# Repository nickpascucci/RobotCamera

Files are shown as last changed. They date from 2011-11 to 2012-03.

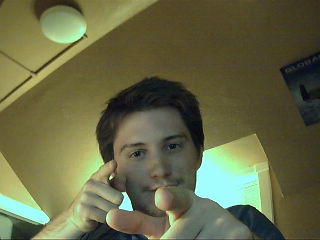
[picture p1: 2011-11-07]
src/victory.jpg

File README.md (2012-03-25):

## Robot Camera

# Overview
This project is aimed at creating a simple rover robot which can use a camera to
identify navigational cues and interesting features when negotiating a maze.

The project consists of a) a set of CAD files used for fabricating the robot's
chasis, and b) source code for motion control, vision, remote operation, and
autonomous navigation.

# Bill of Materials
### Parts:
+ 4 8"x0.75" aluminum right angle extrusion
+ 8 4"x0.75" aluminum right angle extrusion
+ 84 M2.5 x 10 Socket head cap screws
+ 8 M2.5 x 20 Socket head cap screws
+ 92 M2.5 Nuts
+ 1 PandaBoard, with SD card
+ 1 Arduino
+ 2 Continuous rotation servos
+ 2 P1230 Photogates & supporting hardware (refer to your photogate's datasheet.)
+ 1 USB webcam (I used a V7 CS2021.)

### Tools:
+ 3D printer (I recommend using FDM'd ABS for this for its mechanical qualities.)
+ Drill press
+ Soldering iron
+ Tweezers (highly recommended for both soldering and tightening fasteners.)

# How to build this crazy thing
Ok, so you want to build your own robot. How do you get started?

### Structure
First, you're going to need a chasis. There's no reason you have to use mine
versus building your own, but in case you do, all the files you need should be
in the *draw/* directory. All of the parts except for angle aluminum and
fasteners are available as .stl meshes, ready and tested for 3D printing. Most
are also provided as STEP files that can be imported into all major CAD systems
and modified to suit your needs. You'll also need to cut and drill some pieces
of angle aluminum to serve as the primary structural members. I've included
drawings of these parts to give you the right dimensions. All of it goes
together as an assembly as detailed in the assembly.pdf drawing.

### Motion
Great, you have a chassis to hold everything in place. Now you're going to need
some electronics to drive it! The "ServoBracket.{step, stl}" parts are designed
to hold a standard size servo. Of course, a standard servo won't work for
turning wheels; you'll need continuous rotation ones. Mount two of them in the
brackets. In order to keep track of distance traveled and current speed
settings, you'll need to have some kind of encoder on your wheels. I designed a
3D-printable encoder wheel that sits between the servo and the drive wheel. It's
designed to fit into a P1230 photogate, though it should fit others as
well. These can be slotted into the smaller holes on the servo bracket and glued
into place with a 2-part epoxy. Connect the servos and photogates to an Arduino,
modify the firmware to match your pin choices, and upload the
firmware. Congrats, you have a simple motion control system!

### Intelligence
Next comes the brains of the operation. I assume that you made 3 of the board
mount assemblies; if not, do so now. These have little arms that rotate to meet
up with holes in the PandaBoard. Mount your board in the most convenient
orientation; I decided to put the USB ports forward. Attach the Arduino via USB
to the board, and do the same for your webcam. There is a part for mounting a V7
webcam to the chasis; if you have a similar device it should work well, and if
not you'll have to design your own. Attach your webcam to the chasis.

### Software
All right, that just about covers the hardware! Next step, software.

I'll assume that you have a working Linux distribution on your
PandaBoard. You're going to need to install Python (2.7 is preferred), OpenCV
and its Python bindings, PySerial, and Git. Clone this repo onto the PandaBoard,
check that settings.py reflects your configuration, and start up BotDriver. It
will attach to the network interface and wait for a connection from Pilot. On
your control machine, start a Processing session and initiate a Pilot run. Enter
the IP address of the robot and hit "Connect". If everything's working, it
should start feeding you video and relaying your commands to the robot. If not,
something went wrong; look at the output of both Pilot and BotDriver to see if
either of them has any useful information. If not, feel free to get in contact
with me.

## Misc

I'm open to incorporating updates or changes to any of this software/hardware;
if you make any improvements, I'd love to hear about them! If they have any
chance of being useful for other people, send me a pull request and I'll try and
merge them.

## Wishlist
See the issue tracker.

## LICENSE
All of the code in this repository is free software, licensed under the GNU
GPL. If you'd like an alternative license, contact me and we'll work something
out.

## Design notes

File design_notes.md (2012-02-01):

# Design Notes

## Overview

## Hardware Design

### 1) Structure

The system is designed to be constructed from a set of aluminum angle pieces fastened together into
a rectangular box configuration using 3D printed brackets. The source file for these brackets is
available in the draw/ directory. This configuration is straightforward to fabricate and offers
flexibility to the design, as well as an acceptable level of rigidity and ease of modification. 4-40
x 1/2" socket head screws are used as fasteners due to their high availability and their
standardization in mounting circuit boards. Mounting points are provided by additional 3D printed
parts and flat surfaces are fabricated from sheets of acrylic mounted to the frame.

### 2) Locomotion

Movement is accomplished through the use of full rotation servomotors. These motors allow the user
to set a constant angular velocity at the servo shaft via a PWM signal, and are thus useful for
robotics due to their lowered complexity of control. Custom brackets fabricated on a 3D printer are
used to fasten the motors to the frame, and they are controlled by an Arduino microcontroller to
provide a level of abstraction to the main navigation systems.

### 3) Sensing

The system is equipped with several sensors: first, a set of optical rotary encoders measures the
travel of each wheel and reports this data to the Arduino motor controller. This allows the motor
controller to maintain a constant velocity and to record the distance traveled by each wheel,
enabling dead-reckoning position estimates to be performed. Second, a powerful camera assembly is
mounted to the front frame of the robot which provides 640x480 pixel images for use in navigation
and object detection. Image data is transmitted over a serial communications link directly to the
PandaBoard controller, and images can be captured about once every 3 seconds.

### 4) Power Supply

Design of the power supply is ongoing... I've tried using a portable device charger to supply power
over USB, but the PandaBoard draws more current than it can provide and can't complete the boot
sequence. I may combine two such chargers to power the system.

## Software Design
   .......................       ......................
   .                     .       .    Internal        .
   . Input/Sensor Module .........   State Module     .
   .                     .       .  (Kalman Filter)   .
   .......................       ......................
             .                             .
             .                             .
   .......................       ......................         .......................
   .   World State       .       .   Decision         .         .     Actuator        .
   .    Module           .........    Module          ...........      Module         .
   .......................       ......................         .......................

## Notes

- The camera selected for this project was chosen due to its serial communications
  capabilities. Originally, the entire system was to be operated by a Parallax Propeller
  microcontroller; however, the computational requirements of computer vision proved to be too great
  for that system and it was decided to upgrade to a PandaBoard. By that time a camera had already
  been purchased, and the system has been designed to work with it.

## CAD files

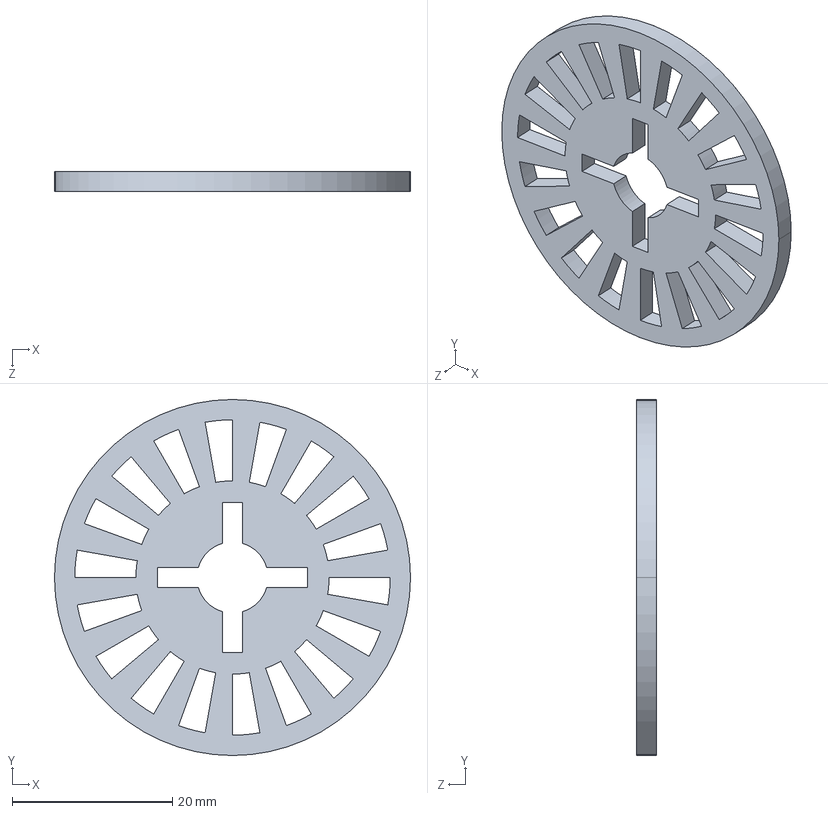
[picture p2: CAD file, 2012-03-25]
draw/step/EncoderWheel.STEP
44.4 x 44.4 x 2.54 mm

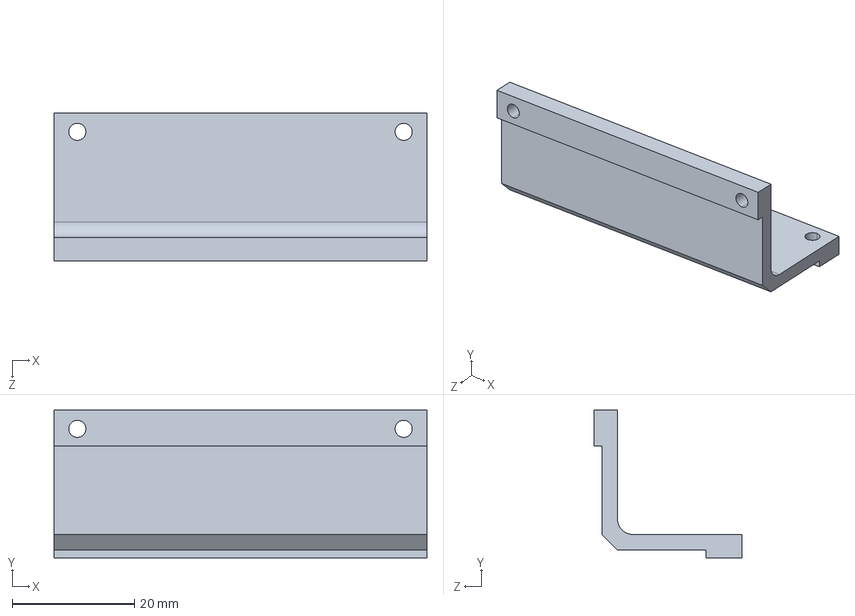
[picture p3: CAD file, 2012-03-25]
draw/step/ServoBracketClamp.STEP
61.0 x 24.1 x 24.1 mm

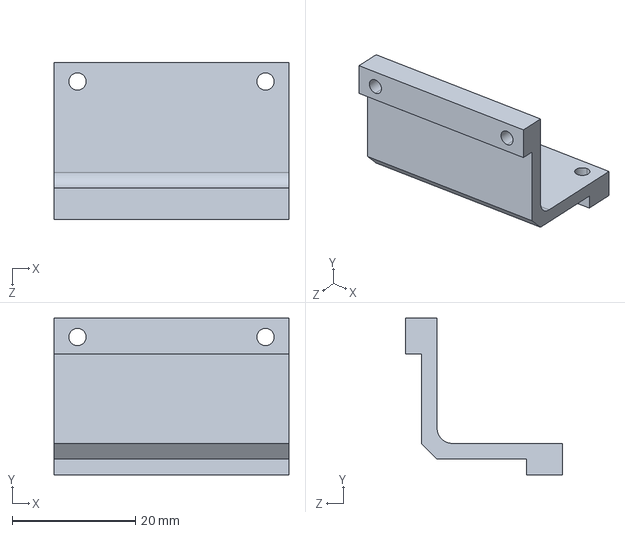
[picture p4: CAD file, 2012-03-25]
draw/step/PartBracketClamp.STEP
38.1 x 25.4 x 25.4 mm

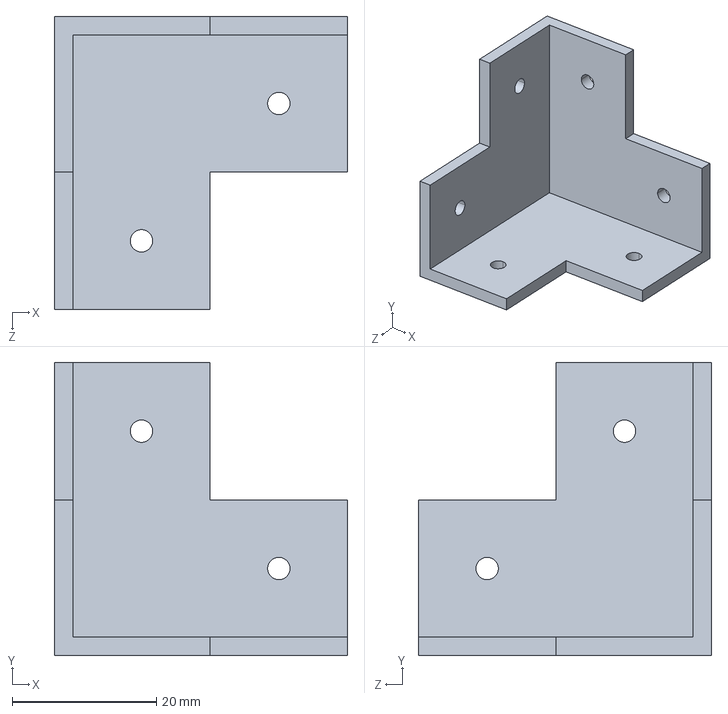
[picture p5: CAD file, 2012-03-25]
draw/step/CornerBracket.STEP
40.6 x 40.6 x 40.6 mm

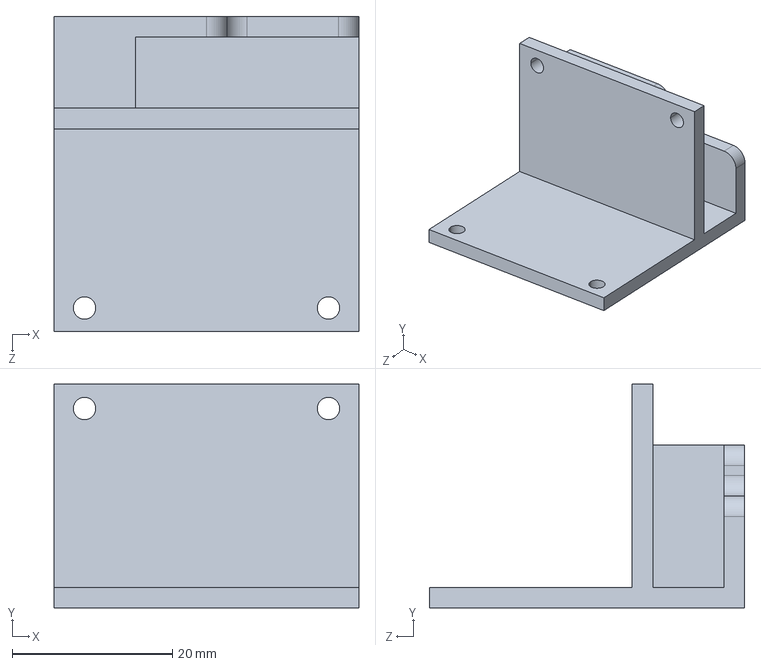
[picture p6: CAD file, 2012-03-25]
draw/step/CameraBracket.STEP
38.1 x 27.9 x 39.4 mm

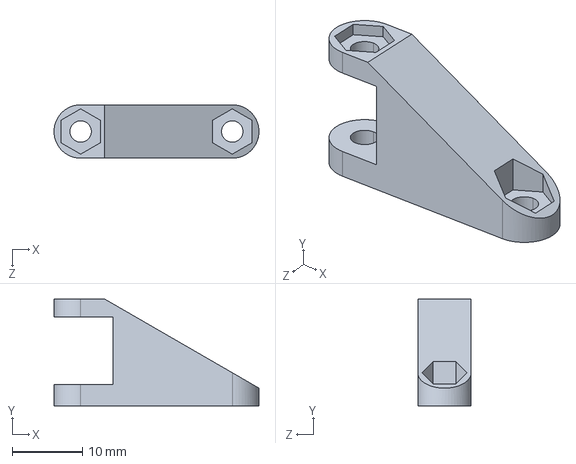
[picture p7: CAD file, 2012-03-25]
draw/step/BoardMountingArm.STEP
29.2 x 15.2 x 7.62 mm

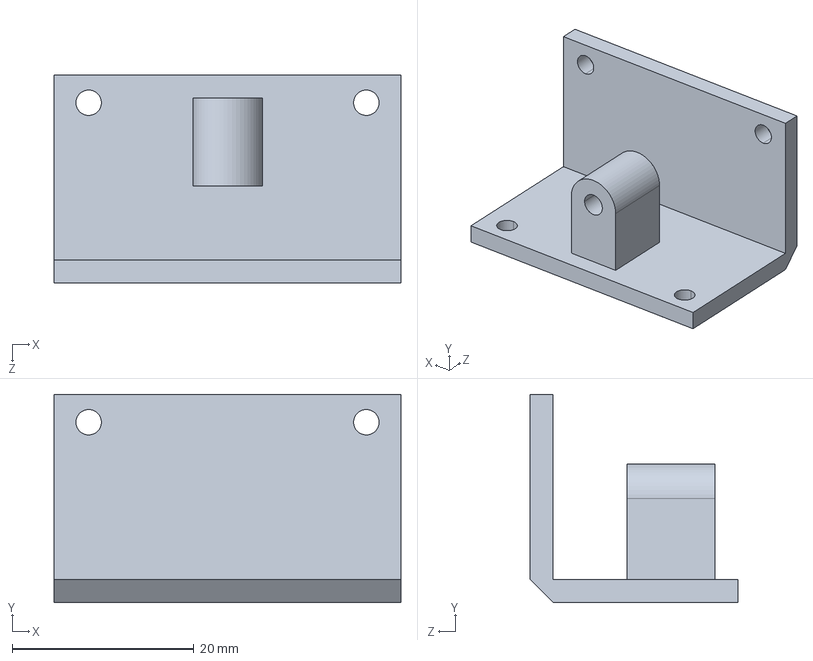
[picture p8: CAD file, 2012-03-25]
draw/step/BoardMountingClamp.STEP
38.1 x 22.9 x 22.9 mm

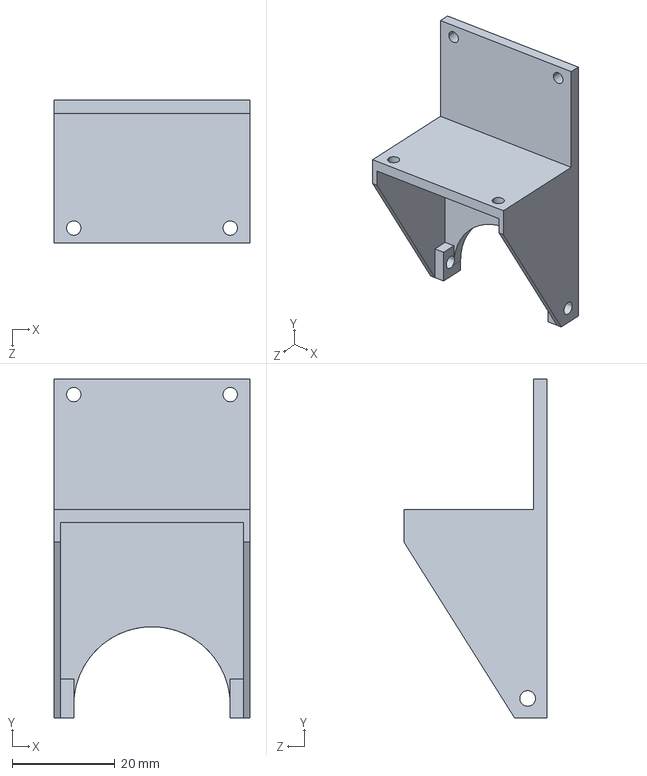
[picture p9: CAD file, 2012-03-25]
draw/step/CasterBracket.STEP
38.1 x 66.0 x 27.9 mm

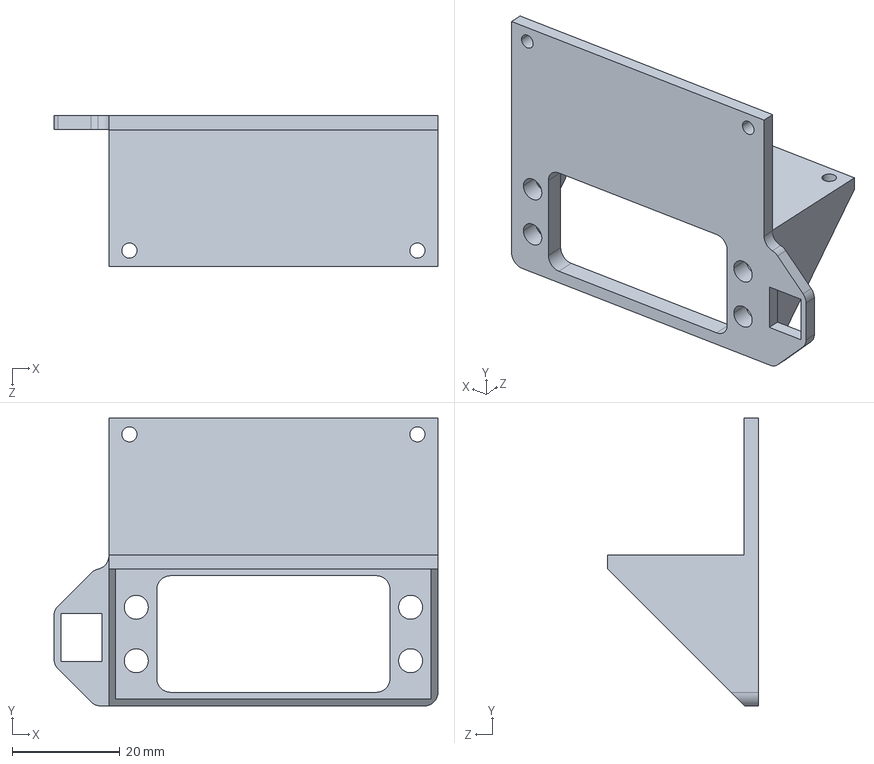
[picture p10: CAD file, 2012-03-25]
draw/step/ServoBracket.STEP
71.1 x 53.3 x 27.9 mm

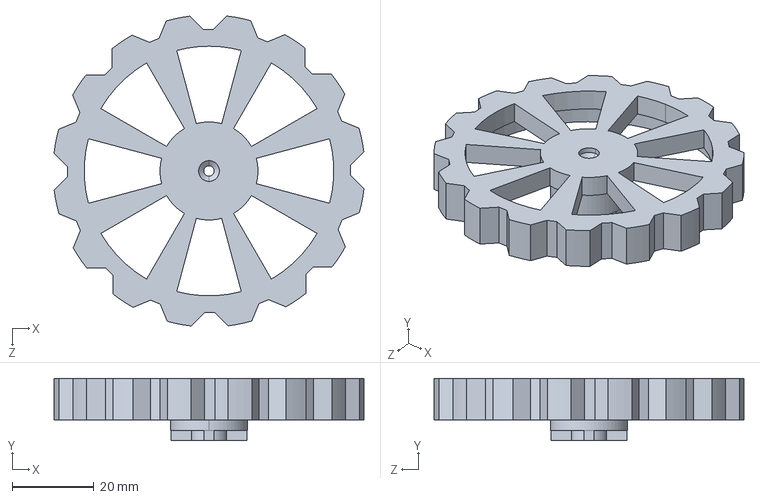
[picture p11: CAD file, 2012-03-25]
draw/step/EncodedTire.STEP
75.7 x 15.2 x 75.7 mm

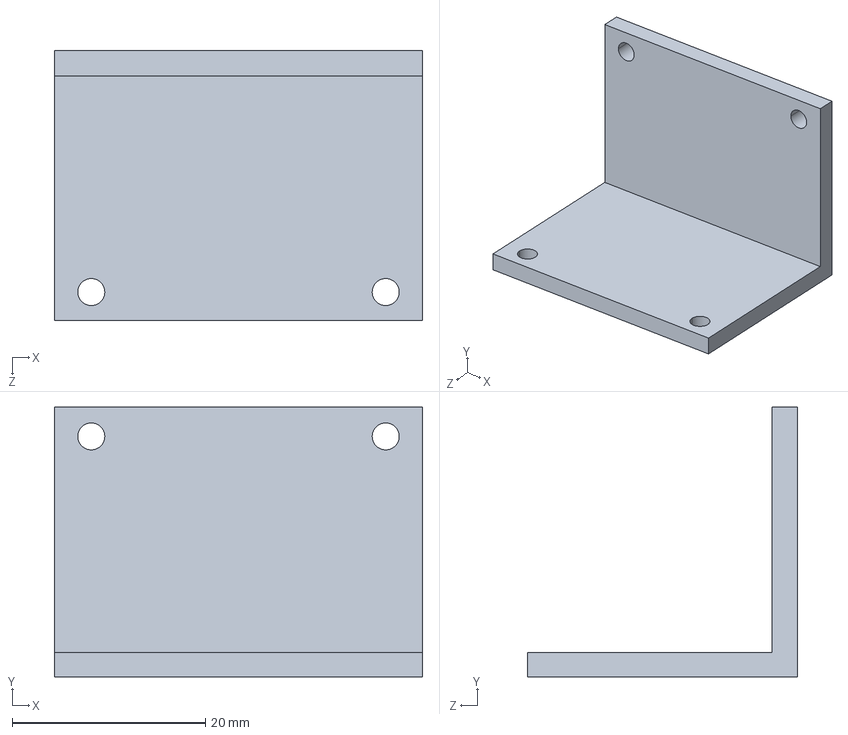
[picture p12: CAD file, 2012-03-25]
draw/step/PartBracket.STEP
38.1 x 27.9 x 27.9 mm

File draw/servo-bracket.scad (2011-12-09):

// Mounting bracket for servos
// Nick Pascucci
// December, 2011

servomount();

module servomount(){
  width = 40;
  thickness = 3; 
  height = 20;
  hole_width = 30;
  hole_height = 12;
  mounting_hole_x1 = 35;
  mounting_hole_x2 = 5;
  mounting_hole_z = 16;
  mounting_hole_size = 2;
  servo_hole_x1 = 37;
  servo_hole_x2 = 3;
  servo_hole_z = 4;
  servo_hole_size = 2;

  difference(){
    base(width, thickness, height, hole_width, hole_height);
    mountingholes(mounting_hole_x1, mounting_hole_x2, 
                  mounting_hole_z, mounting_hole_size);
    servoholes(servo_hole_x1, servo_hole_x2, servo_hole_z, servo_hole_size);
  }
}

module mountingholes(x1, x2, z, size){
  translate([x1, -1, z]){
    rotate([-90, 0, 0]){
      cylinder(h = 5, r = size, center=false);
    }
  }
  translate([x2, -1, z]){
    rotate([-90, 0, 0]){
      cylinder(h = 5, r = size, center=false);
    }
  }
}

module servoholes(x1, x2, z, size){
  translate([x1, -1, z]){
    rotate([-90, 0, 0]){
      cylinder(h = 5, r = size, center=false);
    }
  }
  translate([x2, -1, z]){
    rotate([-90, 0, 0]){
      cylinder(h = 5, r = size, center=false);
    }
  }
}

module base(width, thickness, height, hole_width, hole_height){
  difference(){
    cube([width, thickness, height]);
    translate([(width-hole_width)/2, -1, -1]){
      cube([hole_width, thickness + 2, hole_height+1]);
    }
  }
  
}

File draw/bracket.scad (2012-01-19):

// Parametric bracket for robot chasis.
// Nick Pascucci
// December, 2011

bracket();

module bracket(){
  // Bracket customization parameters
  length = 40;            // Length of each arm
  arm_thickness = 3;      // Thickness of the shell
  arm_width = 23;         // Amount of material in each arm
  hole_d1 = .75 * length; // Distance of hole 1 from the adjacent surface
  hole_d2 = .75 * length; // Ditto, for hole 2
  hole_size = 3;        // Size of all of the holes.

  // Precalculated variables.
  cut_depth = length - arm_thickness;
  hole_offset = arm_width + (length - cut_depth);

  difference(){
    base_cube(length, cut_depth);
    cut_arms(length, cut_depth, arm_width);
    holes(hole_d1, hole_d2, hole_offset, hole_size);
  }
}

module base_cube(length, arm_length){
  hole_location = (length - arm_length) + (arm_length/2);

  difference(){
    cube([length, length, length], center=false);
    translate(v=[length-arm_length, length-arm_length, length-arm_length]){
      cube([arm_length+1, arm_length+1, arm_length+1], center=false);
    }
  }

}

module cut_arms(length, arm_length, arm_thickness){
  translate(v=[-(length-arm_length), -(length-arm_length), -(length-arm_length)]);
  translate(v=[-length, arm_thickness, arm_thickness]){
    cube([2 * length, length-arm_thickness + 1, length-arm_thickness + 1,]);
  }
  translate(v=[arm_thickness, -length, arm_thickness]){
    cube([length-arm_thickness + 1, 2 * length, length-arm_thickness + 1,]);
  }
  translate(v=[arm_thickness, arm_thickness, -length]){
    cube([length-arm_thickness + 1, length-arm_thickness + 1, 2 * length]);
  }
}

module holes(d1, d2, offset, hole_size){
  hole_pair(d1, d2, offset, hole_size);
  rotate([90, 0, 90]) hole_pair(d1, d2, offset, hole_size);
  rotate([-90, -90, 0]) hole_pair(d1, d2, offset, hole_size);
}

module hole_pair(d1, d2, offset, hole_size){
  translate([d1, offset/2, offset/2]){
    rotate([90, 0, 0]){
      cylinder(h=offset, r=hole_size, center=false);
    }
  }
  translate([d2, offset/2, -offset/2]){
    rotate([0, 0, 0]){
      cylinder(h=offset, r=hole_size, center=false);
    }
  }
}

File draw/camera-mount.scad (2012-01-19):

/* -*- mode: c; fill-column: 80; -*- */
// Mounting bracket for camera
// Nick Pascucci
// December, 2011

camera_mount();

module camera_mount(){
  // Customization parameters
  slot_width = 33; // Width of the top of the T slot
  slot_base = 28; // Width of the base of the slot
  slot_thickness = 6; // Height of the slot's two portions in the X
  bracket_depth = 20; // Depth of the bracket slot
  bracket_height = 33; // Height of the entire bracket
  bracket_width = 43; // Width of the bracket in the Y
  bracket_thickness = 5; // Thickness of the bracket interface
  hole_size = 3; // Size of the screw holes
  hole_separation = 20; // Separation of the two holes

  // Precomputed variables
  bracket_length = (2 * slot_thickness + bracket_thickness + bracket_depth);

  difference(){
    cube([bracket_length, bracket_width, bracket_height]);
    translate([0, (bracket_width - slot_base)/2, bracket_thickness]){
      t_slot(slot_base, slot_width, slot_thickness, bracket_height - bracket_thickness);
    }
    translate([2 * slot_thickness + bracket_thickness, 0, bracket_thickness]){
      cube([bracket_depth, bracket_width, (bracket_height - bracket_thickness)]);
    }
    translate([bracket_length - (bracket_depth / 2), bracket_width / 2, bracket_thickness]){
      holes(hole_size, hole_separation, bracket_thickness);
    }
  }
}

module t_slot(slot_base, slot_width, slot_thickness, bracket_height){
  cube([slot_thickness, slot_base, bracket_height]);
  translate([slot_thickness, -(slot_width - slot_base)/2, 0]){
    cube([slot_thickness, slot_width, bracket_height]);
  }
}

module holes(hole_size, hole_separation, bracket_thickness){
  translate([0, hole_separation/2, -bracket_thickness]){
    cylinder(h = bracket_thickness, r = hole_size);
  }
  translate([0, -hole_separation/2, -bracket_thickness]){
    cylinder(h = bracket_thickness, r = hole_size);
  }
}

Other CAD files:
draw/stl/BoardMountingArm.STL
draw/stl/BoardMountingClamp.STL
draw/stl/CameraBracket.STL
draw/stl/CasterBracket.STL
draw/stl/CornerBracket.STL
draw/stl/EncodedTire.STL
draw/stl/EncoderWheel.STL
draw/stl/PartBracket.STL
draw/stl/PartBracketClamp.STL
draw/stl/ServoBracket.STL
draw/stl/ServoBracketClamp.STL

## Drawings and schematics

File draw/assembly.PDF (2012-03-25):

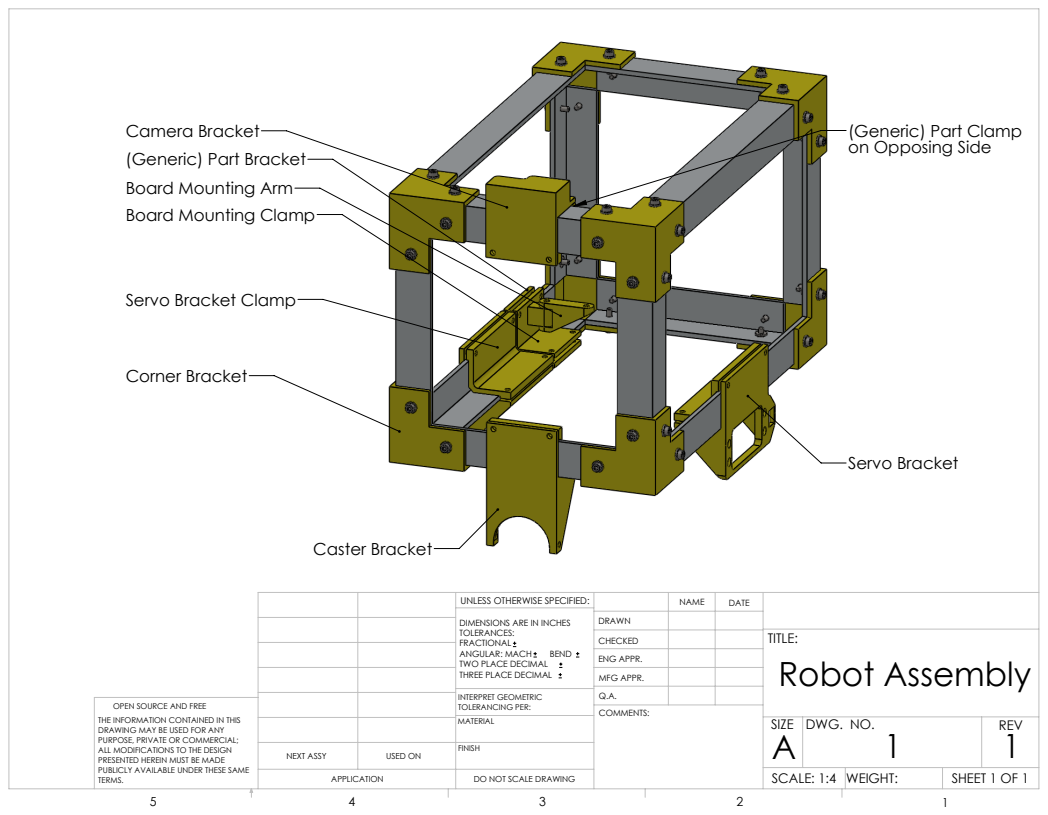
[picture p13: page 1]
Corner Bracket; Caster Bracket; Servo Bracket; Robot Assembly; SHEET 1 OF 1; SCALE: 1:4 WEIGHT:; DWG. NO.; REV; MFG APPR.; ENG APPR.; INTERPRET GEOMETRIC TOLERANCING PER:; ANGULAR: MACH; BEND; NEXT ASSY; USED ON

Camera Bracket
on Opposing Side (Generic) Part Bracket
Board Mounting Arm
Board Mounting Clamp

(Generic) Part Clamp

Servo Bracket Clamp

UNLESS OTHERWISE SPECIFIED:

DIMENSIONS ARE IN INCHES
TOLERANCES:
FRACTIONAL
TWO PLACE DECIMAL
THREE PLACE DECIMAL

OPEN SOURCE AND FREE
THE INFORMATION CONTAINED IN THIS
DRAWING MAY BE USED FOR ANY
PURPOSE, PRIVATE OR COMMERCIAL;
ALL MODIFICATIONS TO THE DESIGN
PRESENTED HEREIN MUST BE MADE
PUBLICLY AVAILABLE UNDER THESE SAME
TERMS.

DO NOT SCALE DRAWING

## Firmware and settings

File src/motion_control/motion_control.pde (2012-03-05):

/* -*- mode: c++; fill-column: 100; -*- */
/*
  Simplified motion control Arduino sketch for the robot's servomotors. 

  Commands:
  'b': Reverse move for 1 second.
  'f': Forward move for 1 second.
  'r': Right (clockwise) rotation of ~30 degrees.
  'l': Left (counter-clockwise) rotation of ~30 degrees.
*/

#include <Servo.h>
#include <Streaming.h>
#include "EServo.h"

EncodedServo left_servo;
EncodedServo right_servo;

// Encoder ticks per revolution
const int ticks_per_rev = 20;

// Move time in milliseconds for forward/backward movements
const int mseconds_per_move = 3000;

// Axle speed in RPM for all moves
const int cruise_speed = 18;

// These units don't really matter, as long as they're the same. I used inches.
// Body width, measured from centerline to centerline on the wheels.
const float body_width = 6.5;

// Wheel circumference.
const float wheel_circumference = 2.9;

// ## Movement

void move(bool forward){
  if(forward){
    Serial << "Moving forward." << endl;
    reset_ticks();
    right_servo.servo.write(right_servo.forward_point);
    left_servo.servo.write(left_servo.forward_point);

    // Wait for the move to complete
    delay(mseconds_per_move);

    stop();
    // At some point it will be desirable to reconcile both sides and make sure they've moved the
    // same distance. For right now, it's fine that they don't.
    // reconcile_servos(true);
  } else {
    Serial << "Moving backward." << endl;
    left_servo.ticks = 0;
    right_servo.ticks = 0;
    right_servo.servo.write(right_servo.backward_point);
    left_servo.servo.write(left_servo.backward_point);

    // Wait for the move to complete
    delay(mseconds_per_move);

    stop();
  }
  Serial << "Done." << endl;
}

/**
   Bring the servos to agreement, so their number of ticks is equal.
*/
void reconcile_servos(bool forward){
  while(left_servo.ticks > right_servo.ticks){
    // Left servo has moved farther, so fix the left and move the right
    left_servo.servo.write(left_servo.zero_point);
    if(forward) {
      right_servo.servo.write(right_servo.forward_point);
    } else {
      right_servo.servo.write(right_servo.backward_point);
    }
  } 
  stop();
  while (right_servo.ticks > left_servo.ticks) {
    right_servo.servo.write(right_servo.zero_point);
    if(forward) {
      left_servo.servo.write(left_servo.forward_point);
    } else {
      left_servo.servo.write(left_servo.backward_point);
    }
  }
  stop();
  Serial << "Done." << endl;
}

void rotate(bool clockwise){
  // We'll need to know how many ticks to move, so get that first.
  int required_ticks = angle_to_ticks(PI/6);
  // Reset the tick counters; we'll need them to keep track of our current position.
  reset_ticks(); 

  if(clockwise){
    Serial << "Rotating clockwise." << endl;

    // To rotate clockwise, we need to move the right servo backward and the left servo forward.
    left_servo.servo.write(left_servo.forward_point);
    right_servo.servo.write(right_servo.backward_point);

    // We need to keep an eye on both servos at the same time, so while one of them is short, 
    // keep updating.
    while(left_servo.ticks < required_ticks || right_servo.ticks < required_ticks){
      // Once we've reached our goal, stop the servo.
      if(left_servo.ticks >= required_ticks){
        left_servo.servo.write(left_servo.zero_point);
      }
      if(right_servo.ticks >= required_ticks){
        right_servo.servo.write(right_servo.zero_point);
      }
    }
  } else {
    Serial << "Rotating counter-clockwise." << endl;
    // Clockwise is the opposite.
    left_servo.servo.write(left_servo.backward_point);
    right_servo.servo.write(right_servo.forward_point);

    // We need to keep an eye on both servos at the same time, so while one of them is short, 
    // keep updating.
    while(left_servo.ticks < required_ticks || right_servo.ticks < required_ticks){
      // Once we've reached our goal, stop the servo.
      if(left_servo.ticks >= required_ticks){
        left_servo.servo.write(left_servo.zero_point);
      }
      if(right_servo.ticks >= required_ticks){
        right_servo.servo.write(right_servo.zero_point);
      }
    }
  }
  // Can't hurt to make sure we're stopped.
  stop();
  Serial << "Done." << endl;
}

/**
   Calculate the number of ticks required in order to rotate through the given angle.

   Since this is calculated with the center of rotation located equidistant between wheels on their
   shared axis, both wheels must move this number of ticks in order to complete the rotation.

   Angle should be in radians.
 */
int angle_to_ticks(float angle){
  // Remember, circumference = 2 * PI * radius; sector length = angle * radius; and we're working
  // with two circles here, the wheel and the circle that it's traveling on.
  // So, we first calculate the length of the sector we have to traverse. In this case, r is the
  // body width divided by two.
  float sec_length = angle * (body_width / 2);
  // Then we need to get the distance covered by the wheels between each tick.
  float distance_per_tick = wheel_circumference / ticks_per_rev;
  // Finally, we can divide the one by the other to get the number of ticks required.
  // This is going to have some rounding error; but it's going to be small enough that we can ignore
  // it for now. If you really want to know how much it is, it's easy to calculate.
  int num_ticks = sec_length / distance_per_tick;
  return num_ticks;
}

/**
   Stop both servos.
*/
void stop(){
  left_servo.servo.write(left_servo.zero_point);
  right_servo.servo.write(right_servo.zero_point);
}

void reset_ticks(){
    left_servo.ticks = 0;
    right_servo.ticks = 0;
}

/**
   Attach the appropriate interrupts to catch ticks from our encoders.
*/
void attach_encoder_interrupts(){
  attachInterrupt(right_servo.encoder_interrupt, right_encoder_tick, HIGH);
  attachInterrupt(left_servo.encoder_interrupt, left_encoder_tick, HIGH);
}

/**
   Record a right encoder tick.
*/
void right_encoder_tick(){
  right_servo.ticks++;
  toggle(13);
}

/**
   Record a left encoder tick.
*/
void left_encoder_tick(){
  left_servo.ticks++;
  toggle(13);
}

// ## Calibration
// These two variables will be modified in interrupt contexts, so they need to be declared volatile.
volatile int speed_calibration = 0;
volatile long int last_calibration_tick;

/**
   Find the point at which the servos move at a given speed.
*/
int calibrate_servo_speed(EncodedServo target_servo, long speed, float error, bool forward){
  // Start the servo at the given speed. This allows us to go both ways when calibrating, in order
  // to calibrate both sides' servos.
  if(forward){
    speed_calibration = 180;
  } else {
    speed_calibration = 0;
  }
  noInterrupts();
  target_servo.servo.write(speed_calibration);

  // Attach a calibration interrupt which decreases speed every time the encoder ticks
  detachInterrupt(target_servo.encoder_interrupt);
  if(forward){
    attachInterrupt(target_servo.encoder_interrupt, calibration_isr_dec, RISING);
  } else {
    attachInterrupt(target_servo.encoder_interrupt, calibration_isr_inc, RISING);
  }
  last_calibration_tick = millis();

  interrupts();

  // Wait for the speed to be reached, within acceptable error.
  while(abs(interval_to_speed(millis() - last_calibration_tick) - speed) > error){
    target_servo.servo.write(speed_calibration);
  };

  // Clean up by detaching interrupts:
  detachInterrupt(target_servo.encoder_interrupt);

  // Remember to reattach the interrupt, since we can't do it generally here.
  return speed_calibration;
}

/**
   Calculate the current rotation speed in rpm from an encoder tick interval
*/
inline float interval_to_speed(long interval){
  // Rotations per second = (ticks/second) / (ticks/rev)
  float tpm = 60000.0 / interval;
  return tpm / ticks_per_rev;
}

/**
   Calibrate both servos, for all of their control points.
*/
void calibrate_all(){
  Serial << "Calibrating..." << endl;
  // Bringing these parameters down will make the calibration take longer, but will detect smaller
  // errors. Keep in mind that there is a certain level of precision one gets with servos; past a
  // certain point, making the acceptable error smaller just makes you wait longer for the same
  // result. 

  // Start with the zero point.
  left_servo.zero_point = calibrate_servo_speed(left_servo, 0, 0.8, false);
  right_servo.zero_point = calibrate_servo_speed(right_servo, 0, 0.8, true);

  Serial << "Servos zeroed." << endl;

  // Next, the forward cruising speed
  left_servo.forward_point = calibrate_servo_speed(left_servo, cruise_speed, 1, false);
  right_servo.forward_point = calibrate_servo_speed(right_servo, cruise_speed, 1, true);

  Serial << "Servo forward speeds set." << endl;

  left_servo.servo.write(left_servo.zero_point);
  right_servo.servo.write(right_servo.zero_point);

  // Finally, the backward cruising speed.
  left_servo.backward_point = calibrate_servo_speed(left_servo, cruise_speed, 1, true);
  right_servo.backward_point = calibrate_servo_speed(right_servo, cruise_speed, 1, false);
  
  Serial << "Servo backward speeds set." << endl;

  left_servo.servo.write(left_servo.zero_point);
  right_servo.servo.write(right_servo.zero_point);

  attach_encoder_interrupts();

  Serial << "Done." << endl;
  Serial << "Calibration values:" << endl;
  Serial << "--- Left ---" << endl;
  Serial << "Z: " << left_servo.zero_point << " F: " << left_servo.forward_point 
         << " B: " << left_servo.backward_point << endl;
  Serial << "--- Right ---" << endl;
  Serial << "Z: " << right_servo.zero_point << " F: " << right_servo.forward_point 
         << " B: " << right_servo.backward_point << endl;
}

/* 
   Calibration Interrupt Service Routine.
*/
void calibration_isr_dec(){
  last_calibration_tick = millis();
  speed_calibration--;
}

void calibration_isr_inc(){
  last_calibration_tick = millis();
  speed_calibration++;
}

// ## Body functionality

void setup(){
  pinMode(13, OUTPUT);
  digitalWrite(13, LOW);

  Serial.begin(115200);

  // Set up servos. We have some default values for the calibration points, which were obtained
  // using the calibration routine above; if you find they're not working for you, run the
  // calibration again and enter their values here so you don't have to calibrate every time.
  // Calibration values:
  //    --- Left ---      |     --- Right ---
  // Z: 93 F: 84 B: 109   |  Z: 98 F: 107 B: 82

  left_servo.servo = Servo();
  left_servo.servo.attach(5);
  left_servo.encoder_interrupt = 0;
  left_servo.zero_point = 93;
  left_servo.forward_point = 84;
  left_servo.backward_point = 109;

  right_servo.servo = Servo();
  right_servo.servo.attach(10);
  right_servo.encoder_interrupt = 1;
  right_servo.zero_point = 98;
  right_servo.forward_point = 107;
  right_servo.backward_point = 82;

  attach_encoder_interrupts();

  blink(3);
  Serial << "Ready." << endl;
}

void loop(){
  // Read a char from serial buffer,
  if(Serial.available() > 0){
    char cmd = Serial.read();
    // see if they match any of our commands, and execute appropriate functions for each.
    switch(cmd){
    case 'f':
      move(true);
      break;
    case 'b':
      move(false);
      break;
    case 'r':
      rotate(true);
      break;
    case 'l':
      rotate(false);
      break;
    case 'c':
      calibrate_all();
      break;
    case 's':
      stop();
      Serial << "All stop!" << endl;
      break;
    default:
      Serial << "Unknown command " << cmd << "." << endl;
    }
  }
}

// ## Utility functions

void toggle(int pin){
  digitalWrite(pin, !digitalRead(pin));
}

void blink(int times){
  digitalWrite(13, LOW);
  for(int i = 0; i < times; i++){
    delay(250);
    toggle(13);
    delay(250);
    toggle(13);
  }
}

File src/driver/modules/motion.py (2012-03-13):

#! /usr/bin/env python
"""This module provides communications with an Arduino for motion control."""

import serial
import time
import driver.settings as settings

__author__ = "Nick Pascucci (npascut1@gmail.com)"

class ArduinoMotionModule():
    # These must be defined to correspond with the values in motion_control.pde
    ROTATE_CW = 'r'
    ROTATE_CCW = 'l'
    FORWARD = 'f'
    BACKWARD = 'b'
    CALIBRATE = 'c'
    STOP = 's'

    def __init__(self):
        self.port = settings.ARDUINO_PORT
        self.baud = settings.ARDUINO_BAUD
        self._connect()

    def move(self, direction):
        """Move in the given direction."""
        if direction == "FORWARD":
            self.send(self.FORWARD)
        elif direction == "BACKWARD":
            self.send(self.BACKWARD)
        else:
            print "Unkown movement command ", direction

    def rotate(self, direction):
        """Rotate in the given direction."""
        if direction == "CLOCKWISE":
            self.send(self.ROTATE_CW)
        elif direction == "COUNTERCLOCKWISE":
            self.send(self.ROTATE_CCW)
        else:
            print "Unkown movement command ", direction

    def send(self, message):
        """Send a packet over the wire."""
        print "Sending message:", message
        try:
            self.conn.write(message)
        except serial.SerialException as se:
            print "Caught SerialException. Attempting to reconnect in 1 second."
            time.sleep(1)
            self._connect()
            # We'll try to resend the message once we're connected. If this
            # fails, we'll just have to die from the exception.
            self.conn.write(message)

    def close(self):
        """Close the module and perform any clean up necessary."""
        pass

    def _connect(self):
        self.conn = serial.Serial(self.port, self.baud, timeout=1)

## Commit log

2011-12-09 Added scad files for brackets.
    [bracket.scad, servo-bracket.scad]
2011-12-11 Added OpenSCAD file for camera mount.
    [camera-mount.scad]
2011-12-17 Added tool for configuring the camera.
2011-12-18 Added camera tool.
2012-01-19 Updated scad files to fix design errors.
    [bracket.scad, camera-mount.scad]
2012-01-19 Added motion control Arduino sketch.
2012-02-20 Added initial overlay button functionality.
2012-02-20 Fixed some issues with the overlay buttons.
    [pilot.pde]
2012-02-20 Rewrote overlay code to use PNG buttons.
2012-02-20 Enabled video pipeline switching.
2012-02-22 Reorganized firmware and renamed to .pde for Arduino IDE
2012-02-22 Updated botdriver and pilot to use separate video and control sockets.
2012-02-23 Modified botdriver and camera module to encode to JPEG in memory.
2012-02-23 Added ArduinoMotionModule.
2012-02-24 Added servo calibration routines.
2012-02-26 Fixed some errors in motion module and added keys to pilot.
    [motion.py, motion_control.pde, pilot.pde]
2012-02-28 Various bugfixes and refactorings.
    - Moved communications code into its own module.
    - Refactored modules to be top-level attributes of the BotDriver.
    - Added Bluetooth comms to BotDriver.
    - Began work on Pilot's bluetooth support. (Will require more refactoring.)
    - Added checks for camera problems.
    [camera.py, communications.py, motion.py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]
2012-02-28 Refactored OverlayButton into its own class and fixed some bugs.
    [TextButton.java, pilot.pde]
2012-02-28 Added -b command line switch to botdriver.
2012-03-04 Abstracted networking code to conform to SocketAdapter interface and updated Pilot.
2012-03-04 Added diagnostic code for encoders.
2012-03-05 Finished calibration routine.
2012-03-08 Added ability to disable buttons to TextButton.
2012-03-08 Added Bluetooth connection capability to Pilot and fixed some errors in comms module.
    [communications.py, pilot.pde]
2012-03-08 Added metadata to prevent network race conditions when requesting images.
    [communications.py, pilot.pde]
2012-03-08 Fixed camera index bug in botdriver.
2012-03-09 Moved Linksprite camera code and examples into subdirectories.
2012-03-12 Modified botdriver to fix serial disconnect issue.
    [motion.py]
2012-03-12 Fixed papercut: address field now has focus by default.
    [pilot.pde]
2012-03-13 Fixed mistake in botdriver; should now add current dir to import path.
2012-03-25 Added CAD files and updated README.
    [BoardMountingArm.STEP, BoardMountingArm.STL, BoardMountingClamp.STEP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]
